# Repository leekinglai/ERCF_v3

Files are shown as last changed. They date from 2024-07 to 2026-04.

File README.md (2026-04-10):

## Carrot Collective Projects

[ERCT / CottonTail Integrated Buffer](https://github.com/Carrot-collective/ERCT)

[Filametrix Toolhead Cutter](https://github.com/Carrot-collective/Filametrix)

[Blobifier Purge System](https://github.com/Carrot-collective/Blobifier)

[Filamentalist Rewinder Buffer](https://github.com/Carrot-collective/Filamentalist)

### Carrot Collective Affiliates

[Jabberwocky Toolhead](https://github.com/kinematicdigit/Jabberwocky)

[Happy Hare Wiki](https://github.com/moggieuk/Happy-Hare/wiki)

<br />

# Enraged Rabbit Community Project

<p align="center">
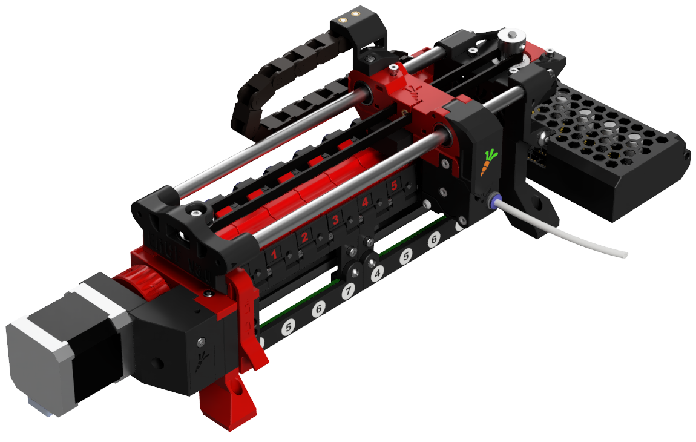
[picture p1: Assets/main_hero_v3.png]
ERCFv3
 
 <h1 align="center">ERCF v3.0</h1>
</p>

<p align="center">
An expandable MMU for Klipper-based 3D-Printers
</p>

<p align="center">
  &nbsp;
  &nbsp;
  &nbsp;
  &nbsp;
  &nbsp;
</p>

<br>

<table>
<tr>
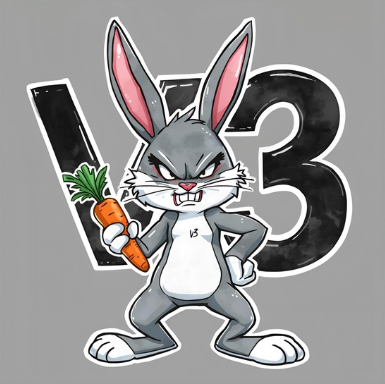
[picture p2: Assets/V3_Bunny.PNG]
Rabbit V3
<td width=30%></td>
<td>
This is a community-born project and a major update to the Voron ERCF MMU that was started a couple of years ago by Ette. It is endorsed by Ette, and the guiding philosophy wasn't to start again with a new MMU design but to refine what has already proven to be a very capable machine and push it to be the best it can be by simplifying problematic construction, improving reliability and aligning as close as possible to v2.0 BOM. The project includes an optional integrated filament buffer system (ERCT), filament cutter option (ERF), a collection of recommended tool head sensor modifications and a bit of Bling! It fully leverages the Happy Hare firmware MMU control software with Klipper Screen extensions.
<p>
 
There is a rapidly growing list of MMUs in the marketplace, from the mass-produced "Fords" who pioneered the market to the "Toyota" that are more recent efficient engineering feat but somehow lacked soul. We consider ERCFv3.0 the "BMW" - a little over-engineered perhaps but distinctively cool, and you feel good driving it. We hope you enjoy it!
</td>
</tr>
</table>

## Table of Content
 
**[ERCF](#enraged-rabbit-carrot-feeder-ercf)**<br>
**[ERCT](#-enraged-rabbit-cotton-tail-erct---filament-buffer)**<br>
**[ERF](#-toolhead-cutter-enraged-rabbit-filametrix-erf)**<br>
**[Toolhead Sensor Modifications](#-toolhead-cutter-enraged-rabbit-filametrix-erf)**<br>
**[Firmware](#firmware)**<br>
**[Documentation](#documentation)**<br>
**[BOM](#bom)**<br>
**[CAD](#cad)**<br>
**[FAQ](#faq)**<br>
**[Acknowledgements](#acknowledgements)**<br>
**[Vendors](#vendors)**<br>
**[Changelog](#changelog)**<br>
**[Build Photos](#build-photos)**<br>
**[Showroom](#user-print-showroom)**<br>
<!--
**[FAQ](Assets/FAQ.md)
-->

<br>

## Enraged Rabbit Carrot Feeder (ERCF)
<table>
<tr>
<td width=45%>An MMU or Multimaterial Unit/Upgrade allows for the automatic change of filaments on your 3D printer. You can use it to create beautiful multi-colored prints or, if you're lazy, simply to avoid loading filament by hand. If you are familiar with ERCF v1.1, this will serve as an overview of updates in v2:</td>
<td>
<ol>
 <li>Sturdy backbone - no more flex</li>
 <li>Reliable (and custom) encoder design</li>
 <li>Sprung servo instead of adjustable top hats</li>
 <li>Innovative Filament trap in blocks instead of magnetic gates</li>
 <li>Formal filament bypass</li>
 <li>Reinforced gearbox assembly</li>
 <li>Beautifully illustrated Manual</li></li>
 <li>High Quality Step-by-step CAD</li>
 <li>Integrated passive buffer system (Cotton Tail)</li>
 <li>Perfect tips with Filametrix Filament cutter</li>
 <li>Functional and aesthetic LED status indication</li>
</ol>
</td>
</tr>
</table>
New features in v3.0 include:
<ol>
 <li>New Direct Drive motor system optimized for torque and ease of use</li>
 <li>Redesigned Gearbox that supports legacy gearing options for upgraders</li>
 <li>Redesigned high-constraint filament blocks with pregate sensors as a default option</li>
 <li>Many Quality of Life additions such as improved Encoder and Selector Cart</li>
 <li>optional microswitch PCBs which allow solderless installation</li>
 <li>optional LED PCBs which allow solderless installation</li>
 <li>Detailed MMB v1.1 and v2.0 wiring diagrams</li>
 <li>Software Setup Documentation for the most popular boards</li>
 <li>Proper GitHub sections for User Mods, Mounting, and PCBs for the community to build upon</li>
 <li>Electronics boxes for the most popular boards: MMBv1 and v2, EasyBRD, ERB*</li>
</ol>

*The ERB is not recommended for use without an additional external 5v power supply.
<br>

## Optional Enraged Rabbit Components

The ERCF ecosystem includes several options to allow you to customize to your specific needs:

#### Filament Buffer/Rewinder Systems
When an MMU changes tool, the unloaded filament needs to be thoughtfully managed so that it doesn't tangle. The ERCF project provides two such systems. The best choice for you will depend on your specific setup:

<br>

###  Enraged Rabbit Cotton Tail (ERCT) - Filament Buffer
<table>
<tr>
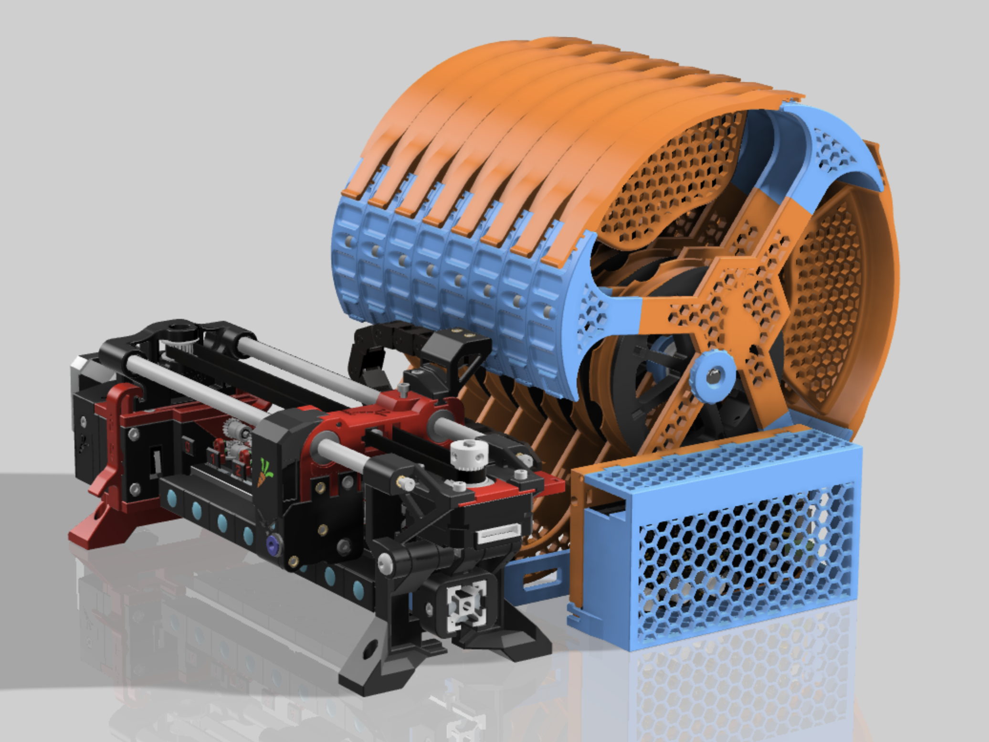
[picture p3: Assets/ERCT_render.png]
ERCT
<td width=30%></td>
<td>
The Enraged Rabbit Cotton Tail (ERCT) buffer system is designed to attach directly to ERCF v3.0. It is a passive system that optimizes space and is also designed to reduce resistance in the filament path, creating a consistent system for calibration.
<p>

ERCT includes a pre-gate filament sensor for automated filament loading and detect runout for endless spool feature. It also incorporates a NEOpixel on each gate that, when driven by the Happy Hare firmware, provides functional feedback and the necessary "bling!"
<p>

ERCT is a very compact and integrated buffer system that is great when your spools are remote from your printer.
<p>

[Read more](https://github.com/Carrot-collective/ERCT) &nbsp;&nbsp; Videos: [Rear Loading](https://youtu.be/9jzB5Un6HKo) [Front Loading](https://youtu.be/GlSXtUkd-b8)
</td>
</tr>
</table>

<br>

###  Enraged Rabbit Filamentalist - Filament Rewinder
<table>
<tr>
<td>
The Enraged Rabbit Filamentalist is an combined solution for buffering AND spool holder and thus provides total space savings. Rather than containing the unwound coils of filament it instead rewinds the filament back onto the spool which means there are never loose filament coils to tangle.
<p>

Filamentalist requires no additional motors because of its innovation of using the gear stepper of the MMU coupled through the filament to power both feeding and rewinding the spool. This can help overcome friction but caution is recommended for really soft TPU.
<p>

Filamentalist can also use the modular pre-gate filament sensor and gate entry LED blocks from ERCT so you don't give up on bling!
<p>

[Read more](https://github.com/Carrot-collective/Filamentalist)
</td>
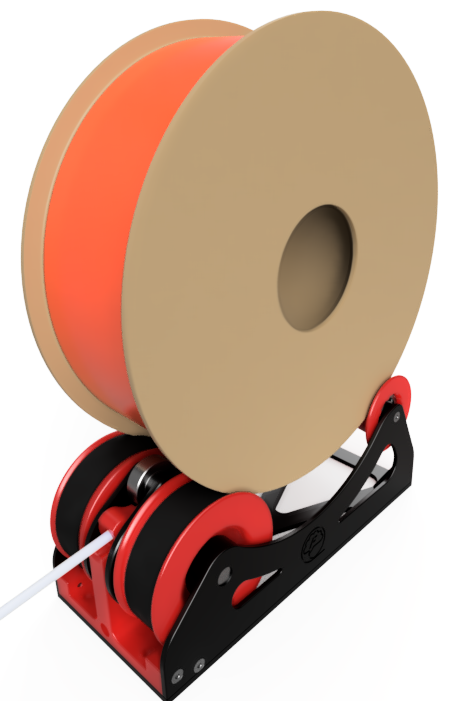
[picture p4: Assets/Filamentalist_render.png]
Filamentalist
<td width=30%></td>
</tr>
</table>

<br>

###  Toolhead Cutter: Enraged Rabbit Filametrix (ERF)
<table>
<tr>
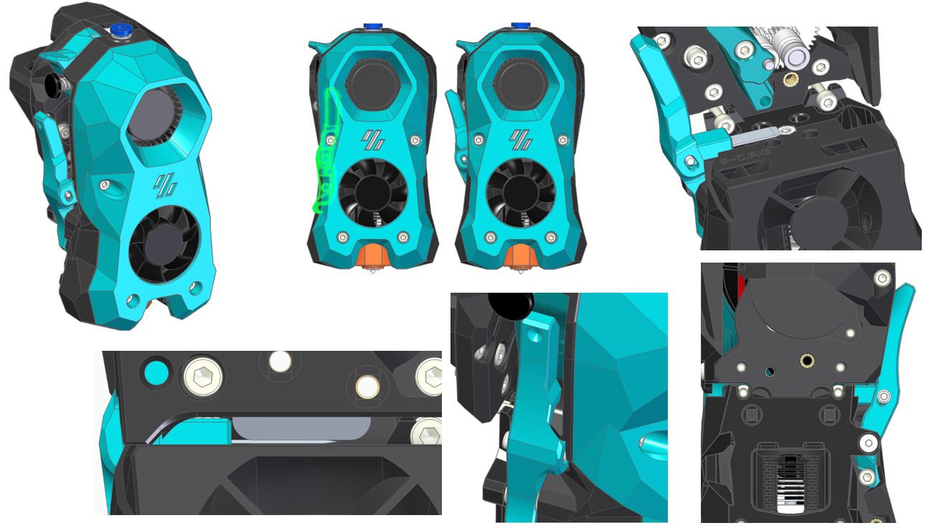
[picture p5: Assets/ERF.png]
ERF
<td width=30%></td>
<td>
Before the MMU can unload a filament, the tip must be prepared so that it can be cleanly loaded next time. This tip-forming process is very difficult to tune and varies based on material type, temperature, hotend type and even weather! Introducing Enraged Rabbit Filametrix (ERF) filament cutting system. This lightweight addition to your Stealthburner toolhead adds a cutting blade. When retracting, the problematic tip of the filament is simply cut off for perfect tips and no jams.
<p>

ERF also supports an optional servo operated ganrtry activation pin so no print area is lost with this addition. ERF designs also include the recommended integrated toolhead sensor
<p>

[Read more](https://github.com/Carrot-collective/Filametrix)
</td>
</tr>
</table>

<br>

###  Toolhead Sensor Modifications
<table>
<tr>
<td>
ERCF can be operated without a toolhead sensor (filament detection) in the toolhead but it is **not recommended**. A toolhead sensor provides an accurate homing point very close to the nozzle but also adds reliability to the tool change process. ERCF includes a set of toolhead sensor modifications for popular extruders. These work reliably through coupling a microswitch to the filament path.
<p>

[Read more](Recommended_Options/README.md)
</td>
</tr>
</table>

<br>

### Purge System (Blobifier)
<table>
<tr>
<td width=30%>Blobifier</td>
<td>

The Blobifier is a small device that eliminates the need for a purgeblock, making filament swaps quicker. It does this by extruding filament onto a tray creating a blob that will get ejected into a purge-bucket.<br />

<h3>Features</h3>

- Turn your filament purge into blobs for less waste and quicker purging.<br />
- Store the blobs in a bucket that can hold 400 blobs!<br />
- Automatically pause the printer once the bucket is full.<br />
- Detect when the bucket is installed or missing.<br />
- Shake the bucket for better dispersion of the blobs in the bucket.<br />
- Clean your nozzle on a brass brush before resuming to print.<br />

[Read More](https://github.com/Carrot-collective/Blobifier)

</td>
</tr>
</table>

<br>

## Firmware
<table>
<tr>
<td width=30%>KlipperScreen</td>
<td>
ERCF is designed to be used with the Happy Hare MMU firmware for Klipper which adds a set of klipper extensions for configuration setup, testing and operation of ERCF. These commands are available through the command line or macros but are perhaps best operated with an interactive UI with the optional KlipperScreen extension.
<p>

Happy Hare provides an easy installation script which has knowledge of recommended settings and will greatly accelerate the setup process.
<p>

[Happy Hare](https://github.com/moggieuk/Happy-Hare/wiki) &nbsp;&nbsp; [KlipperScreen HH Edition](https://github.com/moggieuk/KlipperScreen-Happy-Hare-Edition)
</td>
</tr>
</table>

<br>

## Documentation
<table>
<tr>
<td>
Building something as complex as an MMU is a challenging undertaking, but the ERCFv3.0 project contains an amazingly detailed and illustrated manual with step-by-step instructions. We have tried to make the process similar to fitting together a jigsaw puzzle, albeit with a few optional pieces.
<p>

[Documentation](Documentation)
[Get the latest version of the ERCFv3.0 PDF Manual](Documentation)
</td>
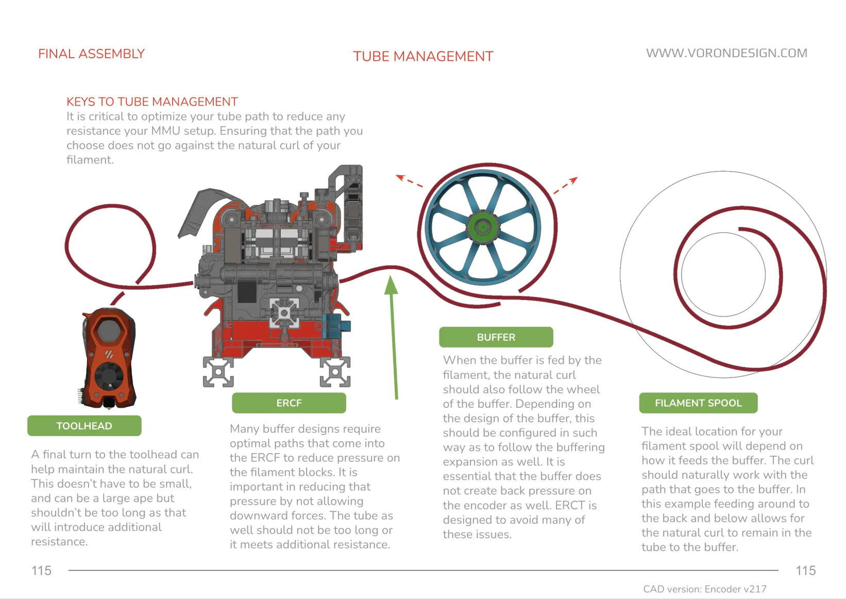
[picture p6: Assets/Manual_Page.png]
ERCF Manual
<td width=30%></td>
</tr>
</table>

<br>

## BOM
<table>
<tr>
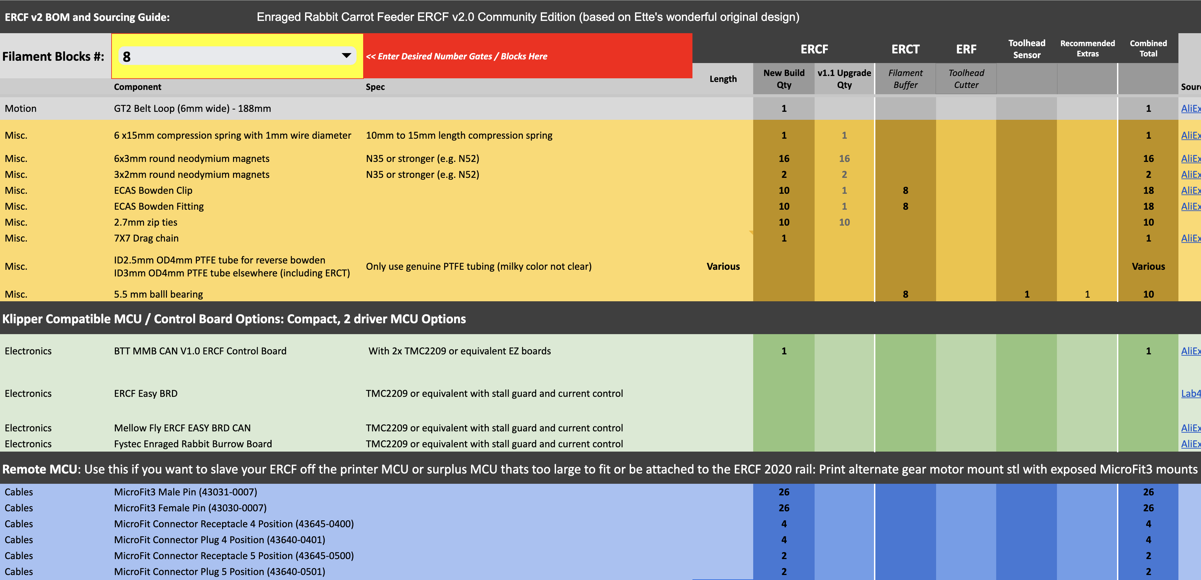
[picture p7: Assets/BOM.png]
ERCF Project BOM
<td width=30%></td>
<td>
You can find a Bill of Materials (BOM) and a convenient printed parts tracker for the project and options here. Note that the BOM also contains an upgrade list for those of you who want to use your existing ERCF v1.1 kits. Please make a copy and edit the "Filament Blocks #" to be the number of gates for your build. This can be any number, but we encourage kit vendors to use 4/8/12 as size variations. Note that there are separate columns for core ERCF, the optional ERCT and ERF options, as well as the suggested "extras"
<p>
Please be aware that the BOM is strictly for reference. The recommended parts can be exchanged for other similar quality parts. Manufacturers who use the BOM as a reference must submit an application for certification before selling them as ERCF v3.0 kits. Please contact us for certification.

[BOM](https://docs.google.com/spreadsheets/d/1UV0rU5Eo4hZX6hcIlSMzn-18oxGSBlLzFjurV6kf8oU/edit?usp=sharing) &nbsp;&nbsp; [Printed Parts Tracker](https://docs.google.com/spreadsheets/d/1MnmpiGlzxnq3sh8Gv73tNb6P1GbJ26OSJ0_e25pumdo/edit?usp=sharing)
</td>
</tr>
</table>

<br>

## CAD
<table>
<tr>
<td>
A lot of work has gone into creating a quality CAD model of the project, carefully organized into folders that match the documentation! It is highly recommended that you open the CAD and hide every folder and then expose them one at a time as you work through the build.
<p>

[Master CAD](CAD)
</td>
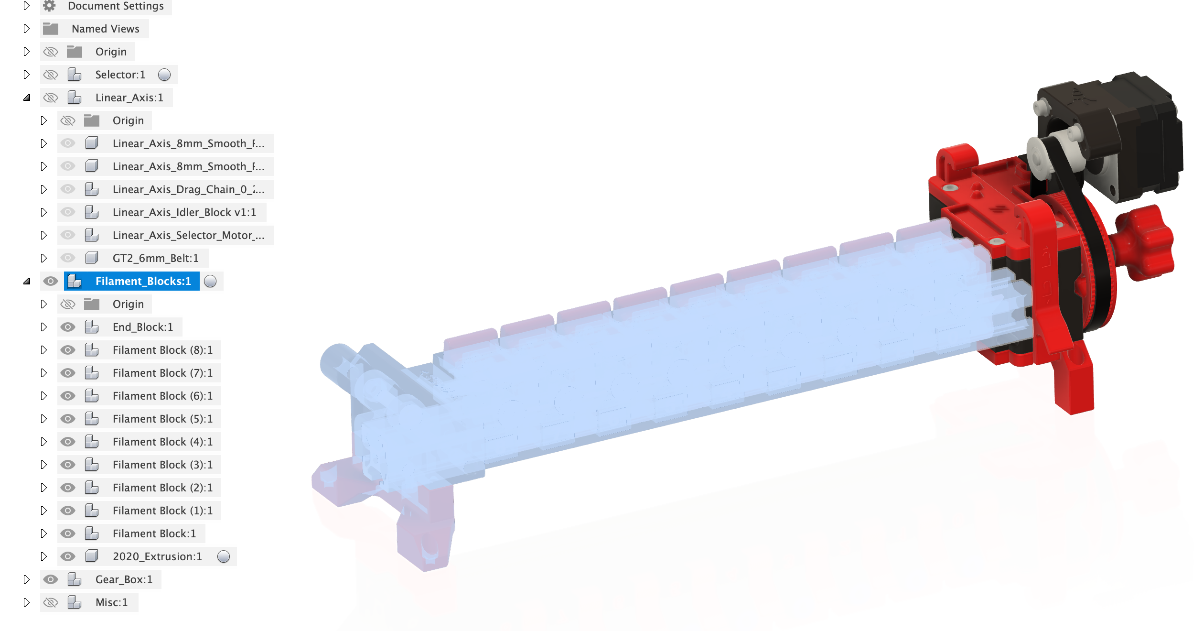
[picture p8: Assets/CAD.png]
ERCF Master CAD
<td width=30%></td>
</tr>
</table>

<br>

## FAQ
ERCF v3 is currently at the fourth iteration or v3.0 phase. Design evolution has required some BOM changes over v2.0. We're sure there will be lots of questions. To avoid repetition on the various support channels, you can find a list of [frequently asked questions](FAQ.md) here. If something isn't answered the best place to go is the primary [ERCF Discord Server](https://discord.gg/t3STJC86HF)

<br>

## Acknowledgements
Most importantly let me introduce the development, test and doc team. A project like this doesn't happen without many hundreds of hours of volunteer effort and all of these folks are truely awesome. Please give some :clap: :clap: :clap:
<ul>
 <li>@Miriax (Designer & Doc Demon)
 <li>@kinematicdigit VS.744 (Designer & Vendor Relations)
 <li>@ningpj (Tester, Breaker & Documenter)
 <li>@SkiBikeMake (Mr Filamentalist)
 <li>@moggieuk V0.1503 | v3.4088 (Mr Happy Hare)
 <li>@gneu v3.0345 (Filament block & bling innovator)
 <li>@sneakytreesnake v3.3804 (The project backbone!)
 <li>@mneuhaus VT.483 (Mr Binky)
 <li>@fizzy (King of CAD)
 <li>@gsx8299 (Test Builder Extraordinaire)
 <li>@sorted (Filametrix "don't get enraged" filament cutting system)
 <li>@kierantheman (Mr ThumperBlocks)
 <li>@Fragmon (Videographer)
 <li>@Silverback v3.1356 (Filametrix tester, builder & engineer)
</ul>

<br>

## Vendors
<table>
<tr>
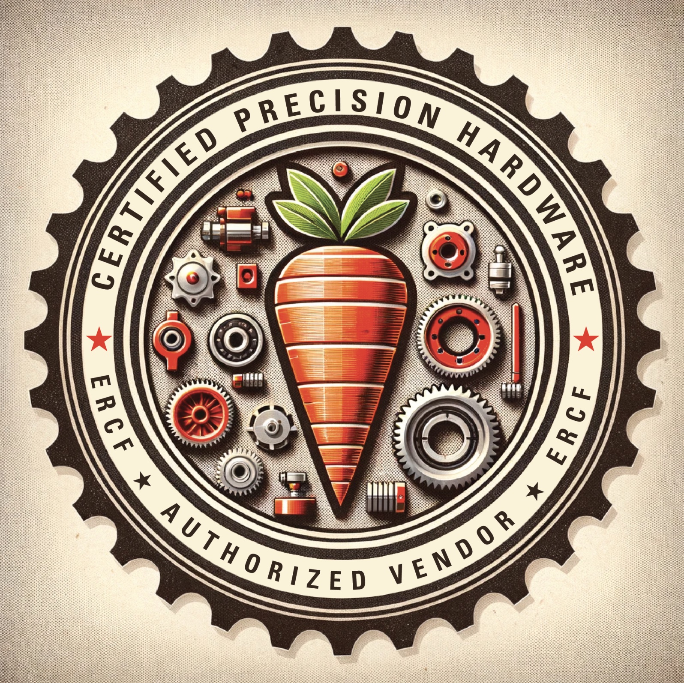
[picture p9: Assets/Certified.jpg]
Vendor Certification
<td width=25%></td>
<td>
These kits and specialty parts will have been checked by us and meet good quality standards. Pending Certification means it has met our first pass inspection and in the process of being verified as a v3 kit. <strong>WE DO NOT RECOMMEND PURCHASING KITS WITHOUT THE CERTIFICATION BY US. PLEASE CHECK BACK HERE FOR THE LIST OF AUTHORIZED VENDORS AND MANUFACTURERS</strong>:<br>
<p>
<ul>
 <li> Approved - Siboor
 </li>
 <li> Pending Submission - Triangle Labs
 </li>
 <li> Approved - <a href="https://www.aliexpress.us/item/3256810002191161.html">Seleadlabs</a>
 </li>
 <li> Pending Submission - Makerpanda
 </li>
 <li> Pending Submission - Fysetc
 </li>
 <li> Approved - <a href="https://www.aliexpress.com/item/1005010543365831.html">Vano3dla 8 channel</a> <a href="https://www.aliexpress.com/item/1005011827763626.html">12 channel</a>
 </li>

 <br>
 <p>
 A list of more official and certified vendors is on the way... stay tuned!
</td>
</tr>
</table>

**Manufacturers:**
_If you want to be included, please contact us. We are happy to validate your kit/parts and then add you to the list._

<br>

## Changelog
<ul>
 <li>v3.0 - Full Release</li>
 <li>v2.0 - Full Release (Happy Easter!)
 <li>v2 RC1 - Initial Release (Happy Christmas!)
</ul>

CAD Design Guidelines used in this project (in case you were interested) can be found: [here](/Assets/Dev_Notes.md).

<hr>

<p align="center"><i>
There once was a printer so keen,<br>
To print in red, yellow, and green.<br>
It whirred and it spun,<br>
Mixing colors for fun,<br>
The most vibrant prints ever seen!
</i></p>

<br>

## Build Photos

Click to enlarge.

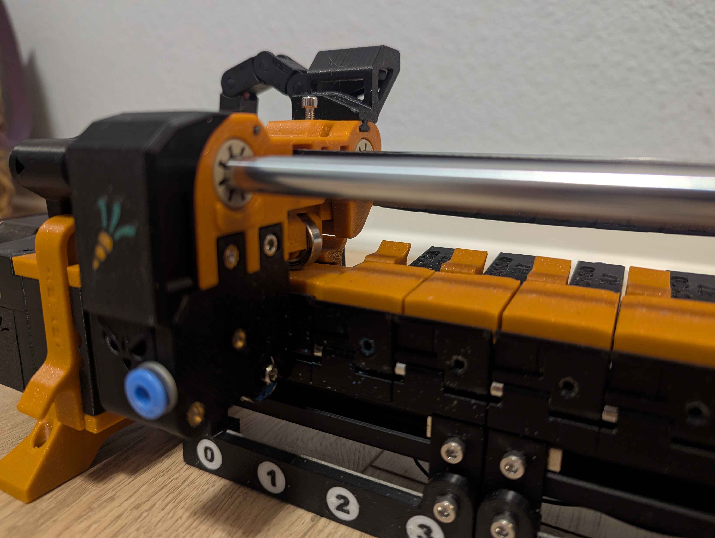
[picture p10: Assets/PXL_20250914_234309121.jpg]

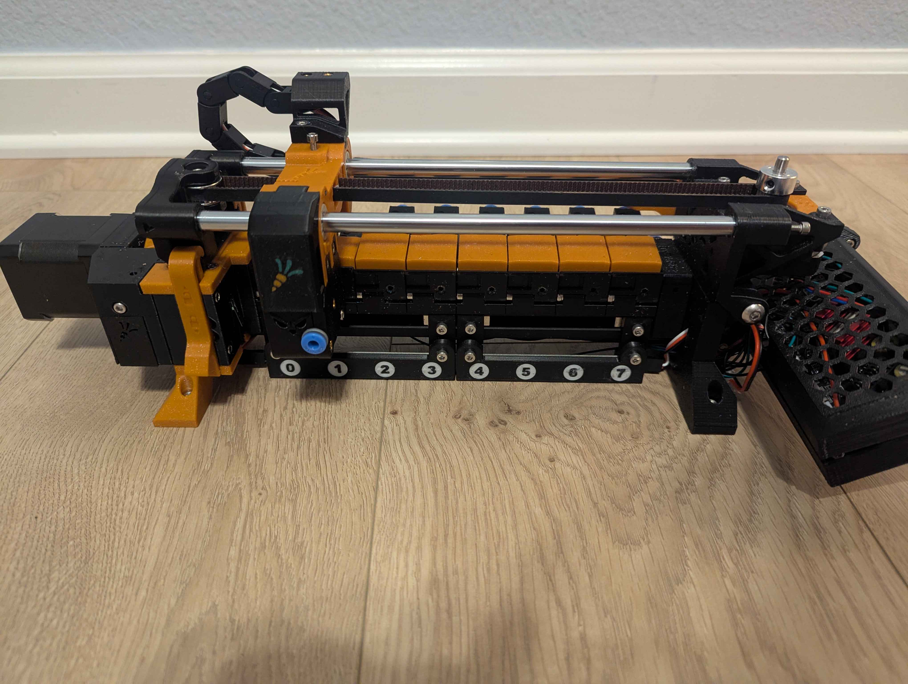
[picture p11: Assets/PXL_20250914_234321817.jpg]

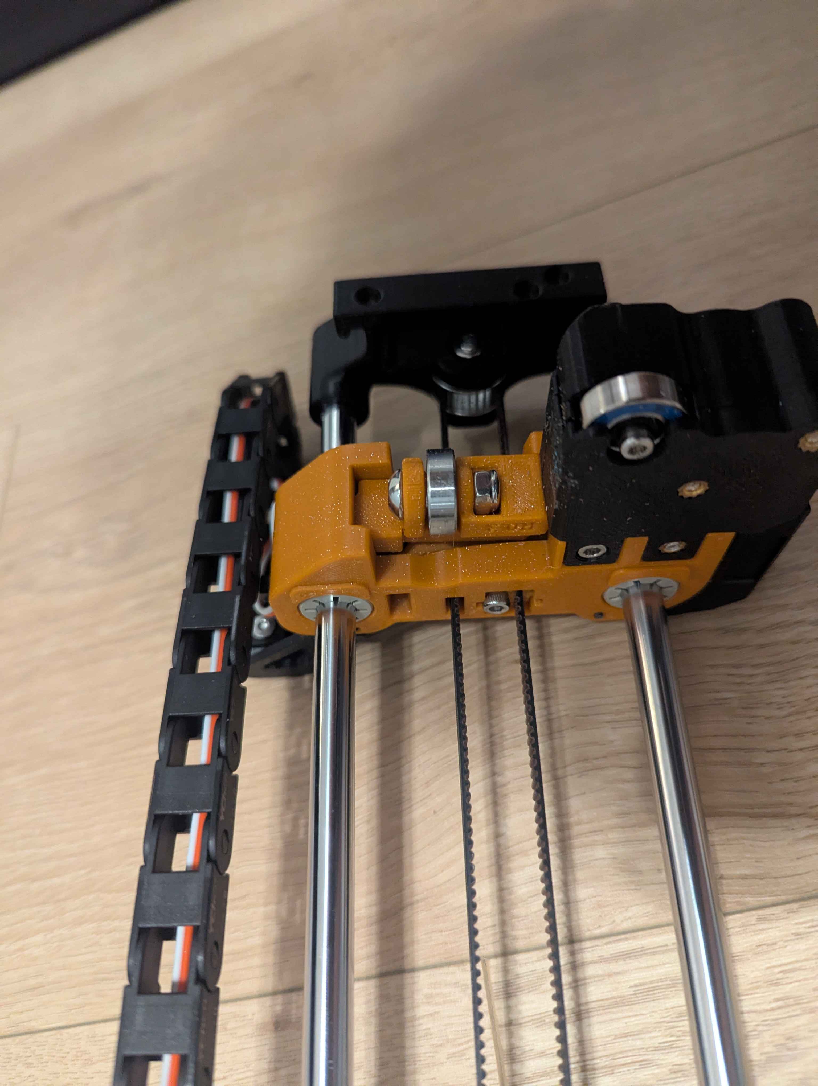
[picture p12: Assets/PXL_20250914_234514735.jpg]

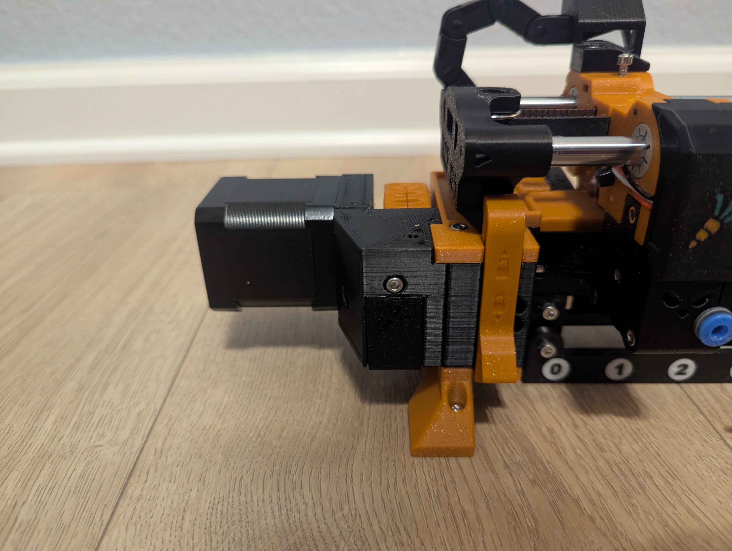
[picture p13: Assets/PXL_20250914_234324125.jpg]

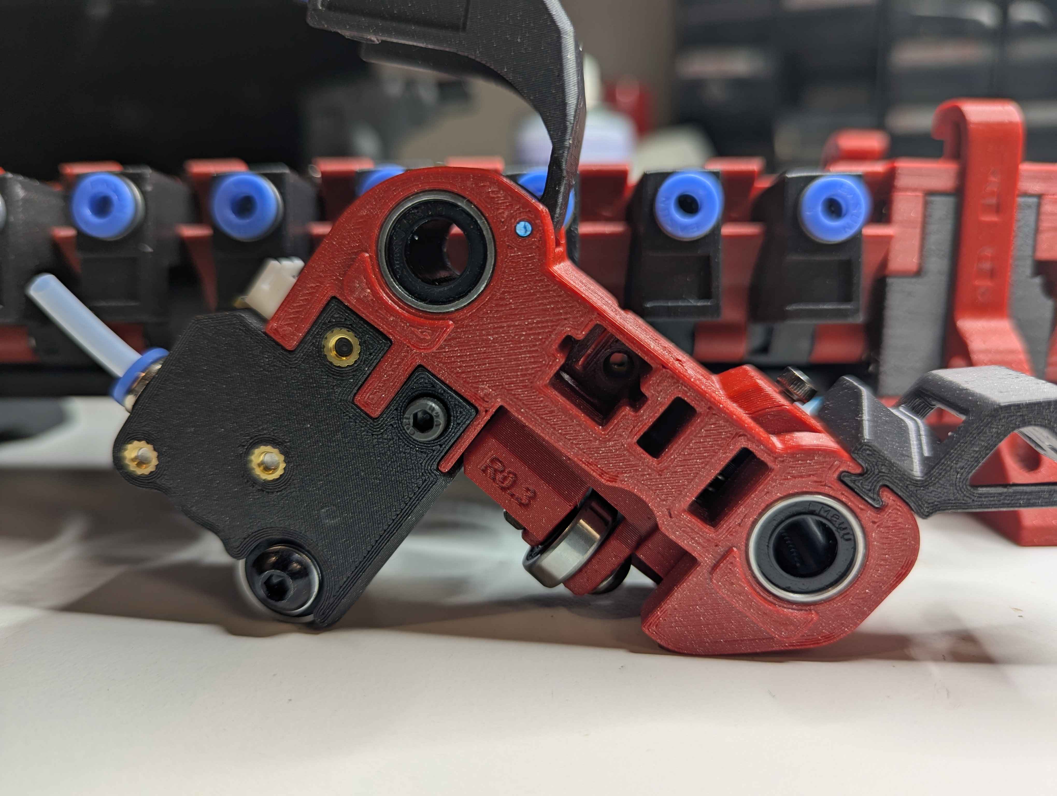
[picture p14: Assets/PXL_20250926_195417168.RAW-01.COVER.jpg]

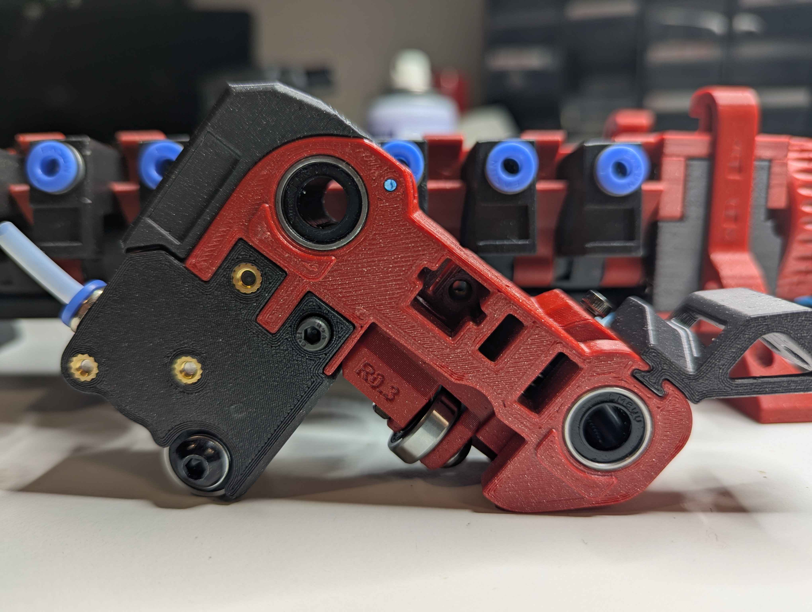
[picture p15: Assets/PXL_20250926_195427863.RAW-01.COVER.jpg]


<br>

## User Print Showroom

Click to enlarge.

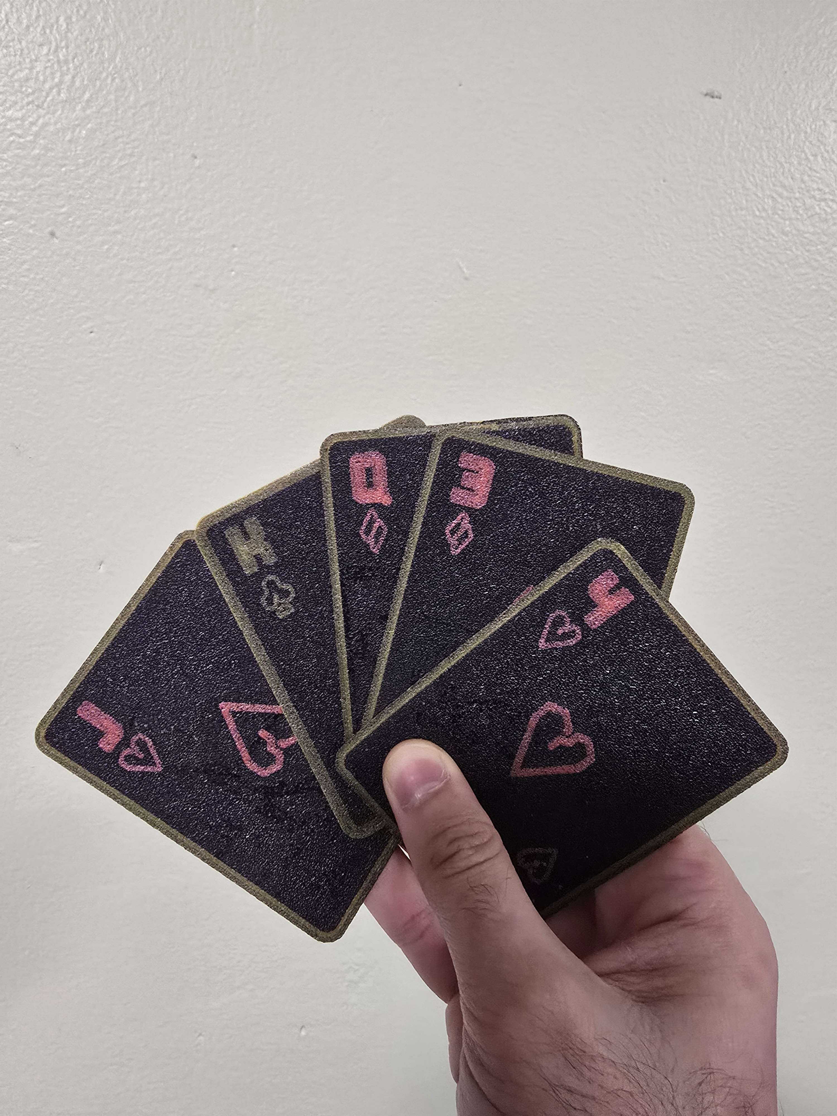
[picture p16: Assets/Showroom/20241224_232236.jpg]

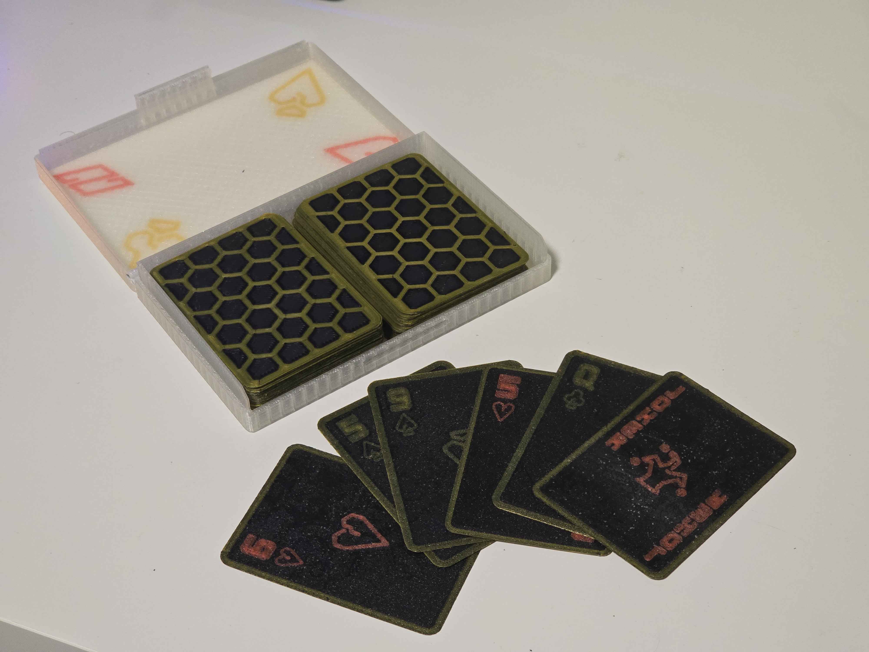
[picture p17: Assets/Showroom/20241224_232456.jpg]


<a href="Assets/Showroom/IMG_4783.png">Gremlin from Mark Norris</a>
<a href="Assets/Showroom/IMG_4783.png">Stormtrooper from Mark Norris</a>

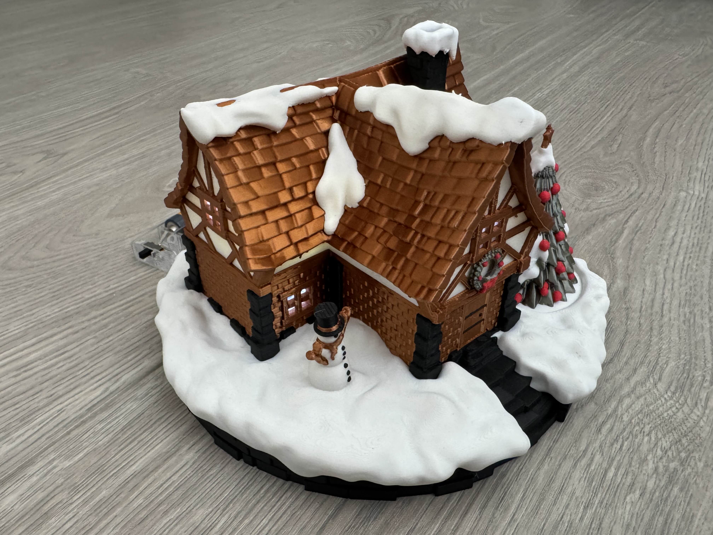
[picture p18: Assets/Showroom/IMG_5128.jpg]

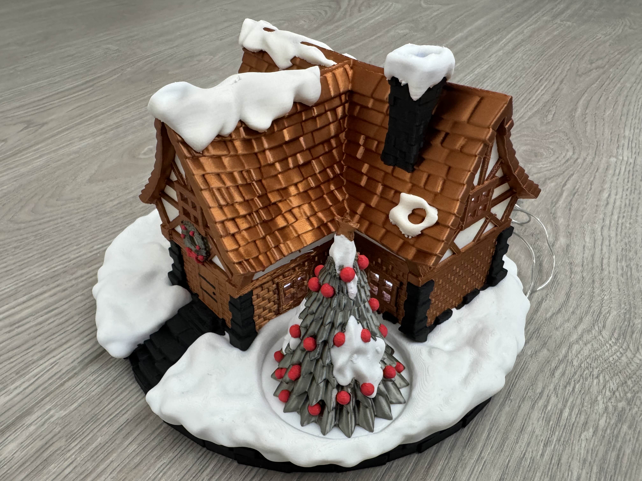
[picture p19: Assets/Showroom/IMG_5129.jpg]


<a href="Assets/Showroom/IMG_5504.jpg">Knit Teddy Bear from Igiannakas</a>
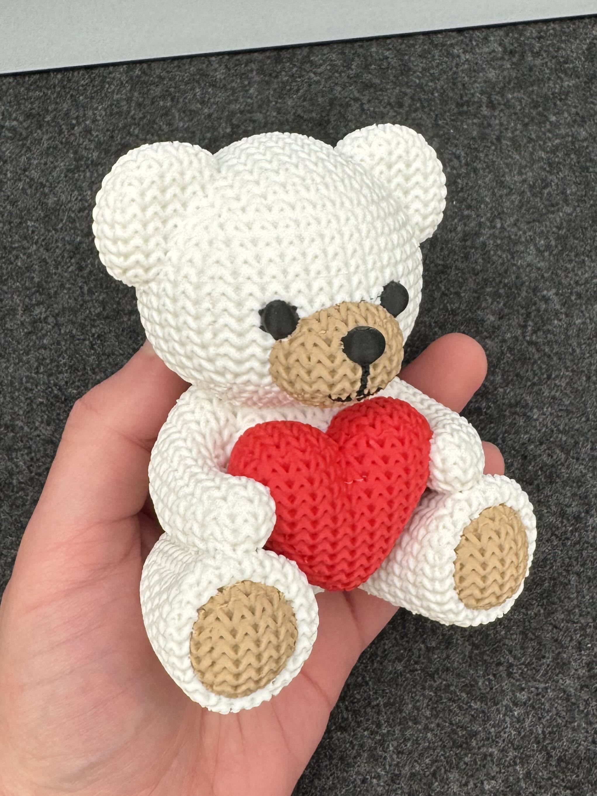
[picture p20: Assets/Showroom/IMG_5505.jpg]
Knit Teddy Bear from Igiannakas


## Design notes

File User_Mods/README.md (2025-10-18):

# ERCF user mod repository

Welcome to ERCF user mod repository. This is a place to share your mods for the ERCF v3 and find useful mods and resources from other ERCF community members.

Mods where the authors have abandoned development can be found in the [`orphaned mods`](./orphaned_mods/) folder. If you want to start maintaining one of them, feel free to reach out via a [GitHub issue](https://github.com/Enraged-Rabbit-Community/ERCF_v3/issues/new/choose).

Looking to submit a mod? Check the [mod submission rules](https://github.com/Enraged-Rabbit-Community/ERCF_v3/blob/main/User_Mods/Mod-Submission-Rules.md) and instructions on [how to submit to ERCF User_Mods](https://github.com/Enraged-Rabbit-Community/ERCF_v3/blob/main/User_Mods/How-to-Submit-to-User-Mods.md)

\[ERCF logo here\]

| Creator | Mod link | Description | Compatibility | Last Changed |
| --- | --- | --- | --- | --- |
| Gneu42 | [Link](Gneu42/Apron_Leds) | Apron LEDs | v2 | Pre-Launch |
| Gneu42 | [Link](Gneu42/Block_End_with_Bushings) | Block End with Bushing | v2 | Pre-Launch |
| Gneu42 | [Link](Gneu42/Drag_Chain_Anchor_With_Microfit3) | Drag Chain Anchor with Microfit3 Connectors | v2, v3 | Pre-launch |
| Gneu42 | [Link](Gneu42/Selector_Drag_chain_Anchor_with_servo_connectors) | Selector Drag Chain Anchor with servo connectors | v2, v3 | Pre-Launch |
| kieraneglin | [Link](https://github.com/Enraged-Rabbit-Community/ERCF_v3/tree/main/User_Mods/kieraneglin/Thumper-Blocks) | Thumper-Blocks | v2 | Pre-Launch
| Miriax | [Link](Miriax/Linear_Axis_Idler_Block_Flipped_Motor) | Flipped Motor Mount for Linear Axis | v2, v3 | Pre-Launch |
| Miriax | [Link](Miriax/Gearbox_for_M6) | Gearbox for M6 Fastener | v3 | Pre-Launch |
| Miriax | [Link](Miriax/Linear_Axis_Idler_Block_for_10mm_Idlers) | Idler Block for 10mm Idlers | v2, v3 | Pre-Launch |
| Miriax | [Link](Miriax/Metal_Coupler_Sleeve) | Metal Coupler Sleeve | v3 | Pre-Launch |
| MNeuhaus | [Link](Mneuhaus/623_Bearing_with_LEDs) | 623 Bearing Encoder with LED | v2 | Pre-Launch |
| MNeuhaus | [Link](Mneuhaus/v623zz_Bearing_with_LEDs) | v623zz Bearing Encoder with LED | v2 | Pre-Launch |
| Batalhoti | [Link](https://github.com/Batalhoti/QuattroSync) | Quattro Sync Tension/Compression Sensor | v2, v3 | 10-18-25 |

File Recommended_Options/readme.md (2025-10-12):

## Recommended Options:

[Filamentalist Rewinder Buffer](https://github.com/Carrot-collective/Filamentalist)

[ERCT / CottonTail Integrated Buffer](https://github.com/Carrot-collective/ERCT)

[Filametrix Toolhead Cutter with Sensors](https://github.com/Carrot-collective/Filametrix)

[Blobifier Purge System](https://github.com/Carrot-collective/Blobifier)

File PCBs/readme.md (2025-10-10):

# PCBs for ERCF

| Creator | PCB link | Description | Compatibility | Last Changed |
| --- | --- | --- | --- | --- |
| Shammy | [Link](Carrot_on_a_Stick) | Carrot on a Stick Apron LEDs | v2, v3 | Pre-Launch |
| Shammy | [Link](Carrot_on_a_Twig) | Carrot on a Twig Apron LEDs | v2, v3 | Pre-Launch |
| TheRogueZeta | [Link](https://github.com/TheRogueZeta/D2F_to_JST_PCB) | D2F to JST PCB | v3 | Pre-Launch |

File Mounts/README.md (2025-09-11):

Mounts for ERCF
---
# ERCF Mounts repository

Welcome to ERCF mounts repository. This is a place to share your mounts for ERCF and find mounts and resources from other ERCF community members.

All mods that apply to older (legacy) ERCF versions can be found in the [`legacy_mounts`](./legacy_mounts) folder.

Looking to submit a mount? Check the [mount submission rules](https://github.com/Enraged-Rabbit-Community/ERCF_v3/blob/main/Mounts/Mount-Submission-Rules.md) and instructions on [how to submit to Mounts](https://github.com/Enraged-Rabbit-Community/ERCF_v3/blob/main/Mounts/How-to-Submit-Mounts.md)

\[ERCF logo here\]

| Creator | Mod link | Description | Compatibility | Last Changed |
| --- | --- | --- | --- | --- |
| Moggieuk | [Link](/Mounts/legacy_mounts/) | Legacy Mounts | v2 | Pre-Launch |

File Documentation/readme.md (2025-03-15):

# ERCF Quickstart

Follow the steps on these pages in order to set up ERCF for the first time!

### ERCF Setup Steps:
- [Flashing Your Local MCU](https://github.com/Enraged-Rabbit-Community/ERCFv2.5/blob/main/Documentation/Flashing-Local-MCU.md)
- [Installing Happy Hare](https://github.com/Enraged-Rabbit-Community/ERCFv2.5/blob/main/Documentation/Installing-Happy-Hare.md)
- [Happy Hare Configuration](https://github.com/Enraged-Rabbit-Community/ERCFv2.5/blob/main/Documentation/Happy-Hare-Configuration.md)
- [Hardware Configuration Checks](https://github.com/Enraged-Rabbit-Community/ERCFv2.5/blob/main/Documentation/Hardware-configuration-checks.md)
- [Hardware Calibration](https://github.com/Enraged-Rabbit-Community/ERCFv2.5/blob/main/Documentation/Hardware-Calibration.md)
- [Toolhead Distances](https://github.com/Enraged-Rabbit-Community/ERCFv2.5/blob/main/Documentation/Toolhead-Distances.md)
- [Installing KlipperScreen Happy Hare](https://github.com/Enraged-Rabbit-Community/ERCFv2.5/blob/main/Documentation/Installing-KlipperScreen.md)
- [Slicer Setup](https://github.com/Enraged-Rabbit-Community/ERCFv2.5/blob/main/Documentation/Slicer-Setup.md)
- [Further Mods to Consider](https://github.com/Enraged-Rabbit-Community/ERCFv2.5/blob/main/Documentation/Further-Mods.md)

#### Even more Happy Hare info can be found at:
- [Happy Hare Wiki](https://github.com/moggieuk/Happy-Hare/wiki)

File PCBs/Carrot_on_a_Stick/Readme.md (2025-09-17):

## Carrot on a Stick LED Board

This board was based on the Disco on a Stick board. The LEDs are spaced 23.05mm, exactly the same as the Filament Blocks, allowing these to be daisy-chained together to make any even number of channels possible with no soldering required!

Thanks to [Blamm!](https://github.com/bartlammers) for allowing us to use his [Disco on a Stick](https://github.com/VoronDesign/Voron-Hardware/tree/master/Daylight/Disco_on_a_stick) design.

Thanks to Shammy and [XR Bunker](https://xrbunker.works/products/carrot-on-a-stick) for modifying the Disco on a Stick design.

Thanks to [Fabreeko](https://www.fabreeko.com/products/carrot-on-a-stick-carrot-on-a-twig-led-boards-for-ercf-v2-0) for being our initial supplier of boards.

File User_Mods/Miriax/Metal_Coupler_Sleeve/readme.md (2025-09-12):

# Metal Coupler Sleeve

Uses 5mm ID "rigid shaft coupling," 20mm long, 12mm diameter, threaded for M4. If you can find one threaded for M3, let me know!

[Amazon.co.jp Link](https://www.amazon.co.jp/dp/B0BZS6CTPC)

[AliExpress Link](https://www.aliexpress.us/item/3256804476993285.html)

[Amazon US Link](https://www.amazon.com/dp/B08V8H721N)

# Print Settings

As normal. Supports are left to the user and not built-in as normal.

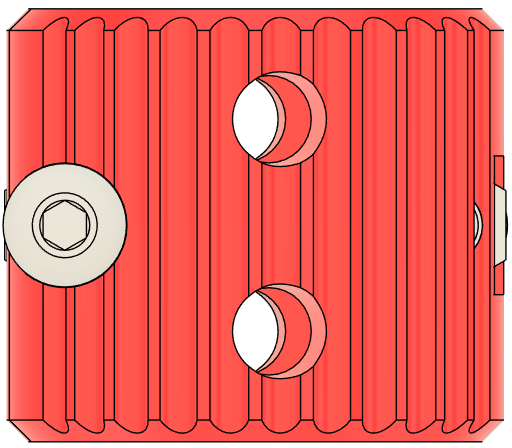
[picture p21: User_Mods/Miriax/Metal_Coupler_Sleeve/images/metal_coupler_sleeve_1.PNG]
coupler angle 1


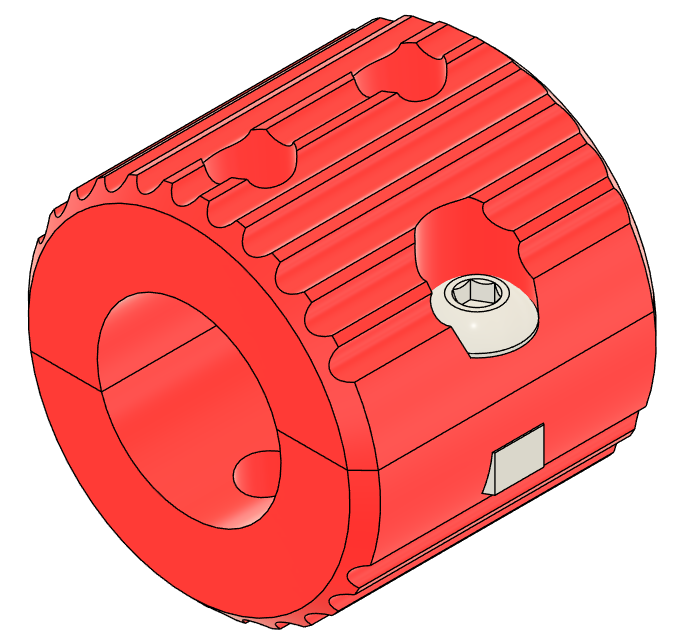
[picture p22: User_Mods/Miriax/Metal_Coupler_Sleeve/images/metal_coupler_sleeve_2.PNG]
coupler angle 2


# Instructions

Insert M3 nut into coupler halves

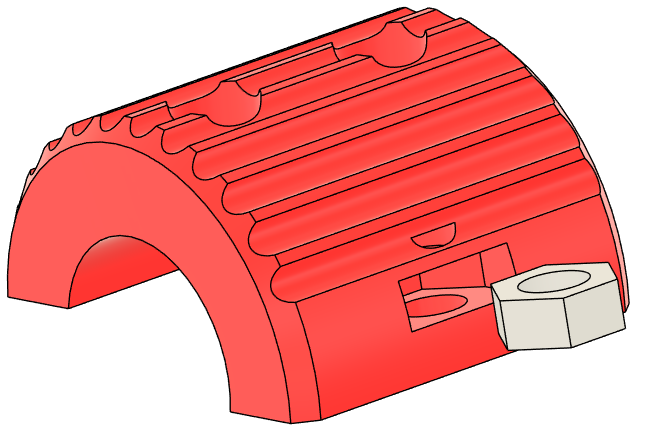
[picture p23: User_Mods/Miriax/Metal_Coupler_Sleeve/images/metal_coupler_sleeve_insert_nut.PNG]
Insert nut into coupler halves


Insert M3x8mm BHCS and snug

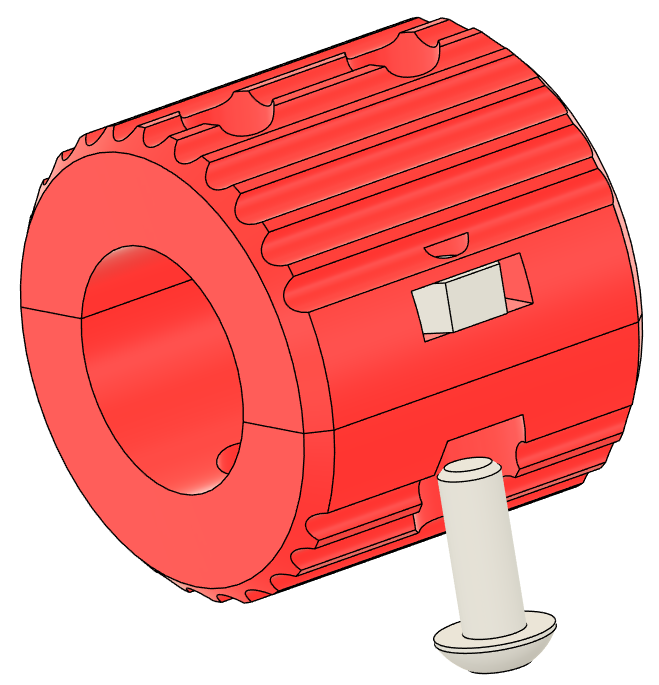
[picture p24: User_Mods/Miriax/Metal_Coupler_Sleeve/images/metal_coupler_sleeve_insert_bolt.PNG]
insert M3x8 bolt and snug


Insert metal coupler. Align the grubscrew holes with the holes in the sleeve. Tighten the bolts, alternating until snug. This only needs to be snug enough to grip the metal coupler.

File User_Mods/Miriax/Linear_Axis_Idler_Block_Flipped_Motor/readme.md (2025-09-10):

This is a Selector Motor mount for Selector motors larger than 20mm. I flipped the motor upside down. It uses all the same hardware. The only difference is that the motor is now 3.8mm closer to the Selector, so you will need to trim ~7.6mm from your belt.

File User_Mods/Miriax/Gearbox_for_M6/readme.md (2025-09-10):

These are Gearboxes for M6 fasteners. One version is for BHCS M6 fasteners (preferred) and the other is for SHCS M6 fasteners.

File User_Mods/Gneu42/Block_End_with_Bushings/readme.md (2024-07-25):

<h1 align="center"><ins>Reinforced Block End </ins></h1>

<H2 align="center">Filament block end with brass bushing and 5mm shaft.</H1>

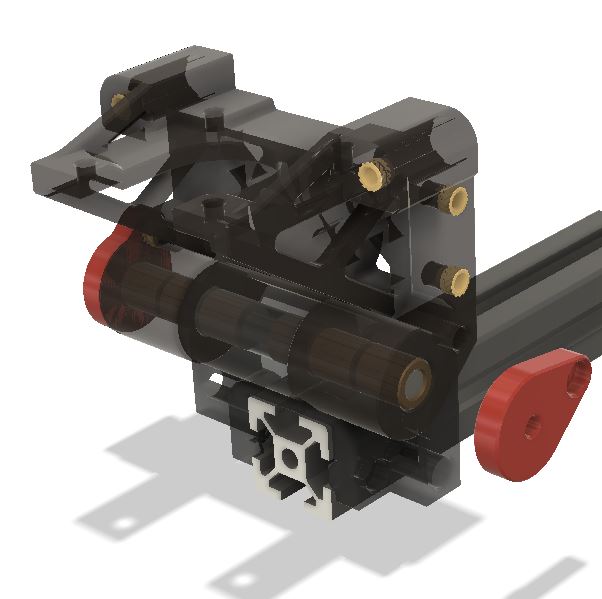
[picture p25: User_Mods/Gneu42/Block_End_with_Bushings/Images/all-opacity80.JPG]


This will give a strong and rigid connection between the top and bottom block end.
It will be very easy to separate the linear axis form the bottom part.
    Just open the exit side Axles stop and push the 5mm shaft with a 2.5mm allen key, and then remove the shaft.

**It will become more useful with the "coming soon" microfit 3 connectors mod that will allow to disconnect the linear axis assembly from the main ERCF.** 

## Bom
In addition to the normal bom for those parts, you will need :
* 2 M3 inserts
* 2 M3x8 SHCS 
* 6 Brass bushings 5x9x10
* 1 Shaft 5mm in diameter, 68mm long.  

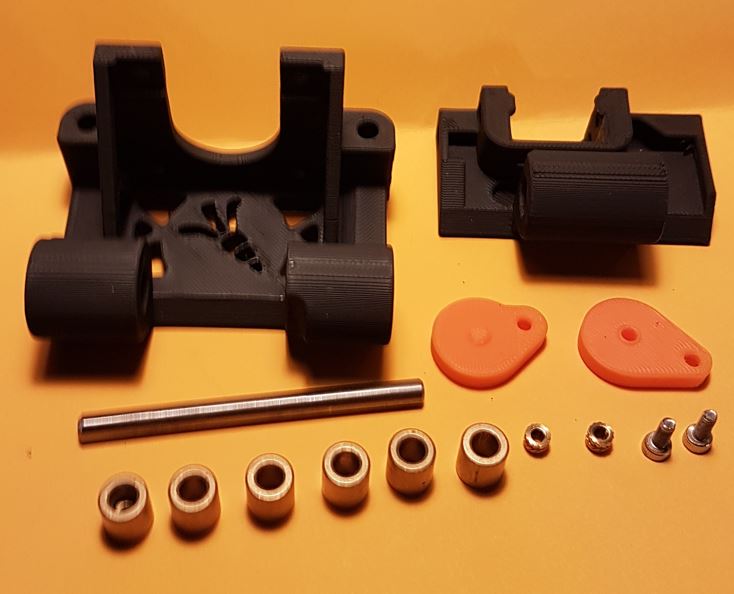
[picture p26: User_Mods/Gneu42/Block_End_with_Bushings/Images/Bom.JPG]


The bushings can be found on Aliexpress : https://fr.aliexpress.com/item/1005004074472637.html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

## Cut view

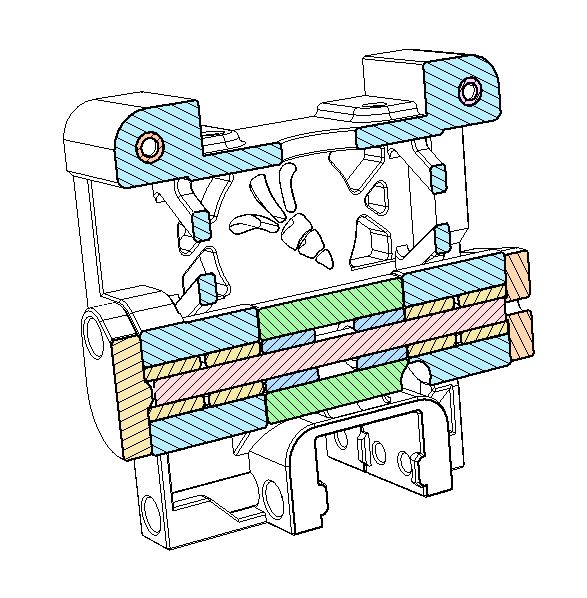
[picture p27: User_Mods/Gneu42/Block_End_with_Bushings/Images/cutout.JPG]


## Images

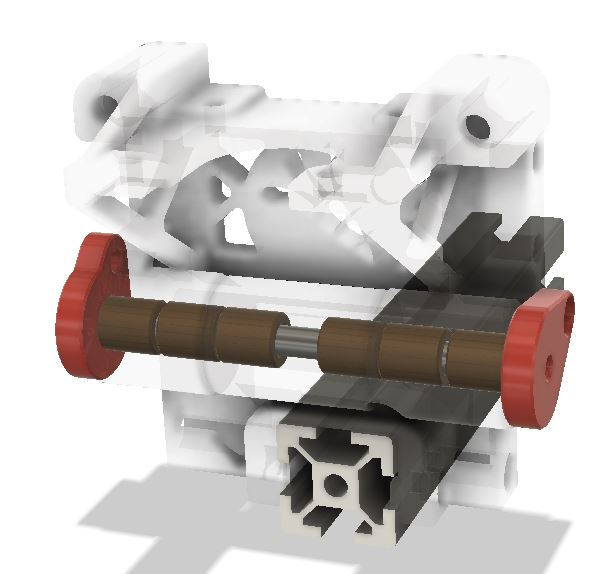
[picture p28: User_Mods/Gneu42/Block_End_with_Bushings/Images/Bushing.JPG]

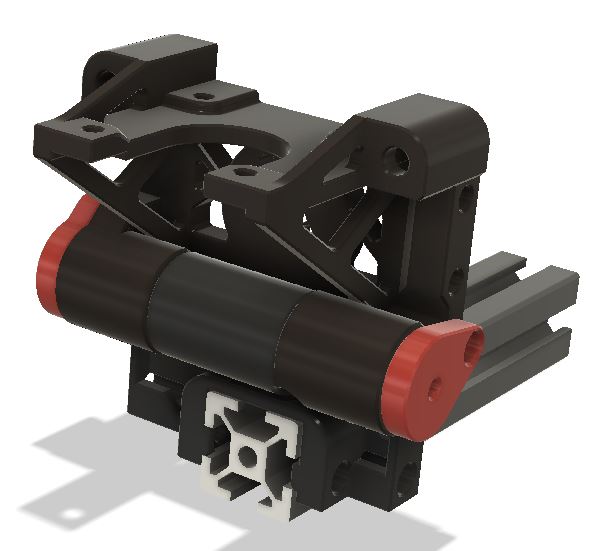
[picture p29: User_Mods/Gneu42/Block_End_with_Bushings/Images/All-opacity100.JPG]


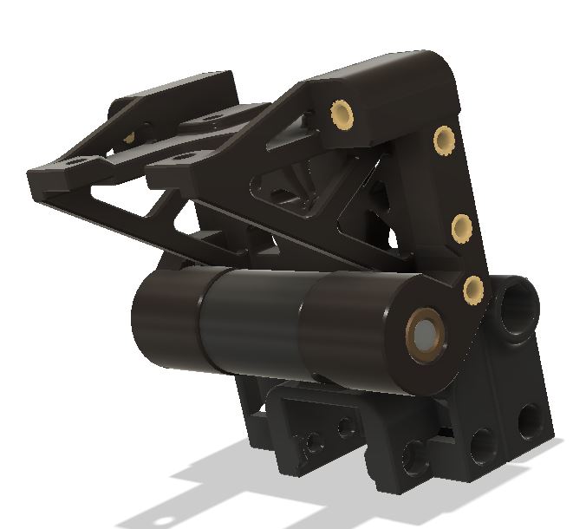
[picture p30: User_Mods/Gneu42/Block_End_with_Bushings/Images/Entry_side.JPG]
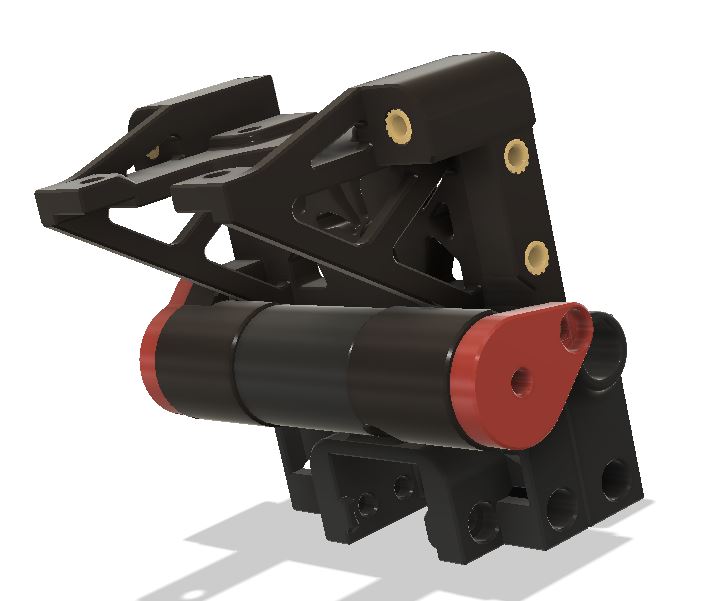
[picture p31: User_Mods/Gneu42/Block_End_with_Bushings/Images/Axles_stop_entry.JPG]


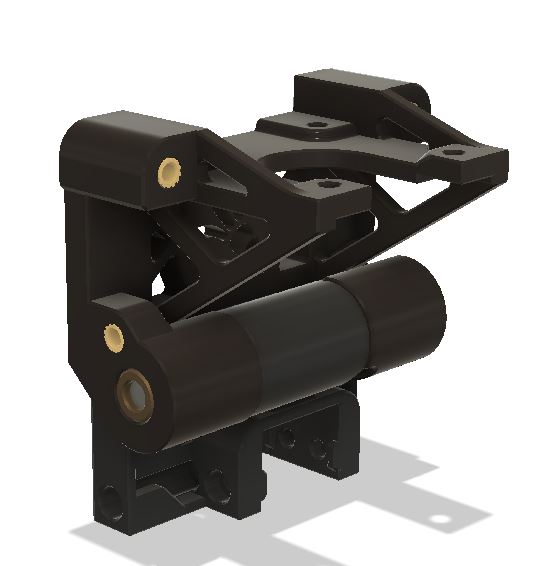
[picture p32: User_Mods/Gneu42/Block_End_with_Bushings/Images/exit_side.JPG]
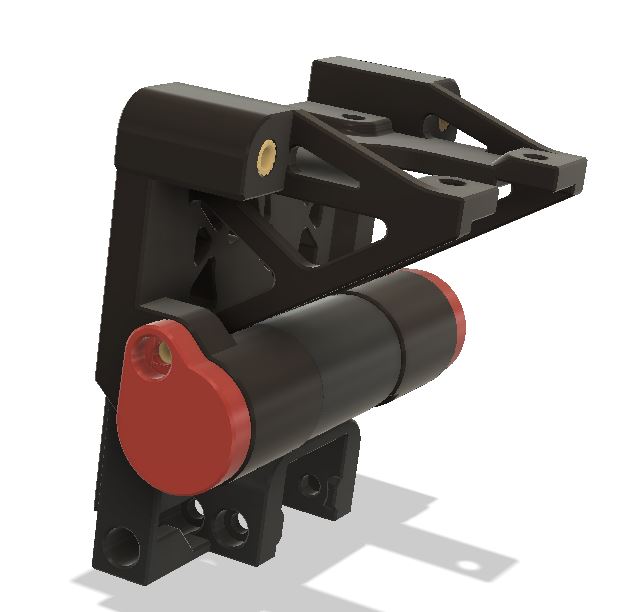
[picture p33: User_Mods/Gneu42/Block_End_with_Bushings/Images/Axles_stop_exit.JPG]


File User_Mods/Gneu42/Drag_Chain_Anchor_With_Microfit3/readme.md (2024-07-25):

<h1 align="center"><ins>Darg chain anchor with Microfit 3 connectors </ins></h1>

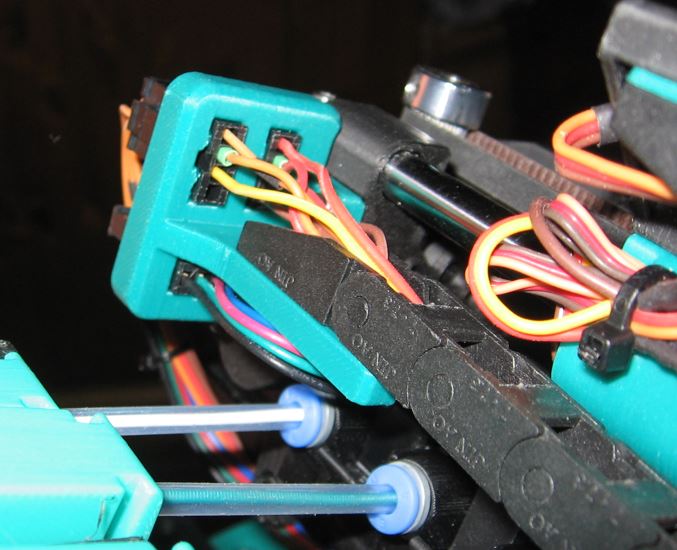
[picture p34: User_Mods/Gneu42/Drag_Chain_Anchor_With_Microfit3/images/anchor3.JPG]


This will allow to very easily remove the top part of the ERCF V2 for maintenance purpose.
It is designed to go with the Block End with bushing mods on this repo.

## Bom
In addition to the normal bom for those parts, you will need :
* 2 M3 inserts
* 2 M3x8 SHCS 
* 3 Microfit 3, 4 pins connector male
* 3 Microfit 3, 4 pins connector female  

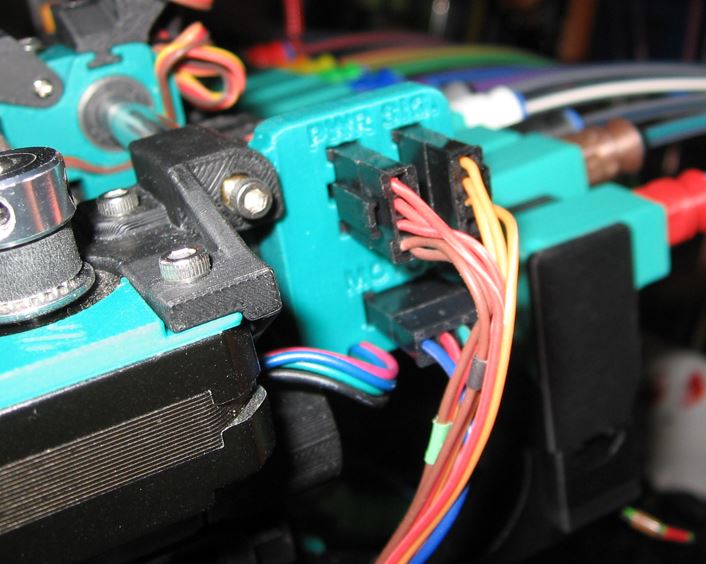
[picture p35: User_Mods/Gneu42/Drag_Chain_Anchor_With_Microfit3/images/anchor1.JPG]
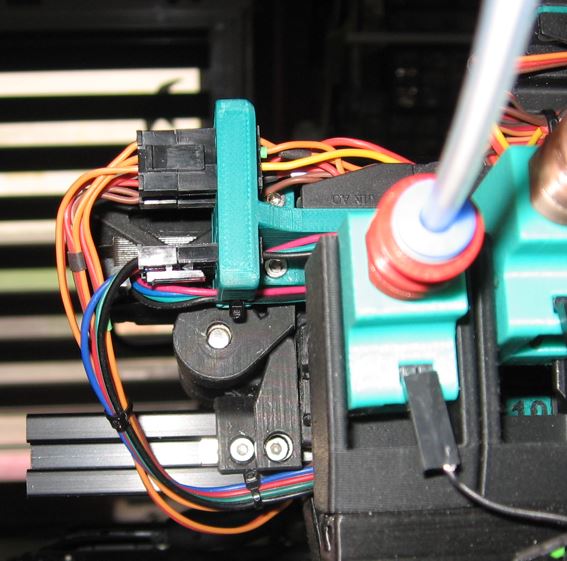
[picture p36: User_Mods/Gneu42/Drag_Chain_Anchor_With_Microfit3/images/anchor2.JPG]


* The connector marked "MOTOR" is used for the motor connection
* The connector marked "PWR" is used for power supply of the Binky encoder, the servo, and the status LED.
* The connector marked "Sig." is used for the signals of the Binky encoder, the servo signal, the status data signal of the status LED, and a spare pin available for what ever you need more. 

**Here is an example of the Microfit3 pinout :**

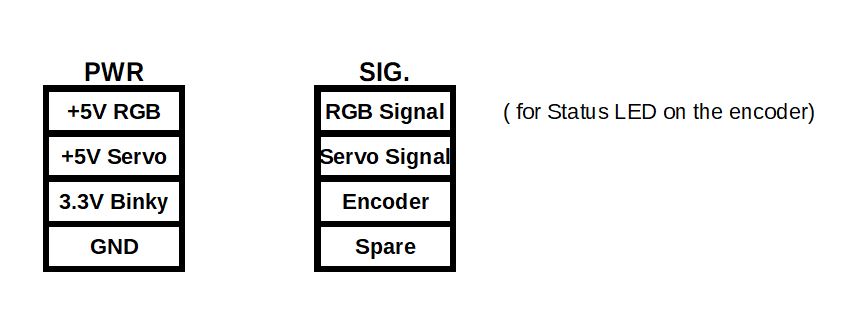
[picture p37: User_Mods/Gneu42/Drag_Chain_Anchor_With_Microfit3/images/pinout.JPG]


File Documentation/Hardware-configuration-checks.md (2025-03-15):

#### Page Sections:
  - [Checks You Should Have Done Already](#checks-you-should-have-done-already)
  - [Step 1. Check Endstop & Optional Sensors](#step-1-check-endstop--optional-sensors)
  - [Step 2. Check motor movement and direction](#step-2-check-motor-movement-and-direction)
  - [Step 3. Check the Encoder](#step-3-check-the-encoder)
  - [Step 4. Check other sensors (if fitted)](#step-4-check-other-sensors-if-fitted)
  - [Step 5. Check Servo](#step-5-check-servo)

*\[This guide was adapted from the [Happy Hare Wiki](https://github.com/moggieuk/Happy-Hare/wiki) for ERCF v2.5. Thanks Moggie!\]*

## Checks You Should Have Done Already

All of these checks and adjustments were covered in the Build Manual, and should have been done while building your ERCF.

-Filament path / BMG Gear alignment (Manual page 71)

-(if using a Geared setup) Adjustment of GT2 pulley and belt tension (Covered in the Geared Drive sub-Manual)

-Encoder path adjustment (page 114)

-Setting GT2 pulley and belt tension (page 127)

-Setting 8mm rod depth (page 136)

**If you haven't done these steps, go review the manual!**

<br>

Now that you've completed the [Happy Hare Configuration](https://github.com/Enraged-Rabbit-Community/ERCFv2.5/blob/main/Documentation/Happy-Hare-Configuration.md), you should be greeted by a large warning on your console:

```yml
Prerequsite calibration steps are not complete:
Use MMU_CALIBRATE_SELECTOR to calibrate selector for gates: 0,1,2,3,4,5,6,7
Use MMU_CALIBRATE_GEAR (with gate 0 selected) to calibrate gear rotation_distance on gate: 0
Use MMU_CALIBRATE_ENCODER (with gate 0 selected)
Use MMU_CALIBRATE_GEAR (with gate selected) or MMU_CALIBRATE_GATES GATE=xx to calibrate gear rotation_distance on gates: 1,2,3,4,5,6,7
Use MMU_CALIBRATE_BOWDEN
```

That is normal, do not worry. Before we tackle that, we need to make sure all of the hardware is configured correctly!

## Step 1. Check Endstop & Optional Sensors

Verify that the Selector endstop, and any installed extruder or toolhead sensors are working. The recommended procedure is:

`MMU_MOTORS_OFF`

Now remove filament from ERCF and extruder, and move the Selector to the center of travel.

`QUERY_ENDSTOPS`

(Or use the visual query in Mainsail or Fluuid). Validate that you can see:

```yml
mmu_sel_home:open
extruder:open
toolhead:open
[...]
```

> [!NOTE]
> You will only see the sensors you have installed. You will additionally see any endstops or sensors installed on your printer.

Then manually press and hold the selector microswitch and rerun `QUERY_ENDSTOPS`.

Validate that you can see `mmu_sel_home:TRIGGERED` in the list.

If you have an extruder sensor installed, feed filament into the extruder past the switch and rerun `QUERY_ENDSTOPS`.

Validate that you can see `extruder:TRIGGERED` in the list.

If you have a toolhead sensor installed, feed filament into the toolhead past the switch and rerun `QUERY_ENDSTOPS`.

Validate that you can see `toolhead:TRIGGERED` in the list.

If any of these don't change state, then the pin assigned to the endstop is incorrect. If the state is inverted (i.e. enstop transitions to `open` when pressed) then add/remove the `!` on the respective endstop pin in `mmu_hardware.cfg`. 

Other endstops like "touch" operation and pregate sensors are advanced and are not cover by this inital setup.

## Step 2. Check motor movement and direction

Once pins are correct it is important to verify direction.  It is not possible for the installer to ensure this because it depends on the actual stepper wiring.  The recommended procedure is:

Run the command `MMU_MOTORS_OFF` Now move the Selector to the center of travel. 

Next, run the command `MMU_HOME` and verify that the Selector moves towards the endstop / home position

If the Selector doesn't move it is likley that the pin configuration for `step_pin` and/or `enable_pin` are incorrect. Open up `mmu_hardware.cfg`, and find the section `[stepper_mmu_selector]`.

Verify the pin names and prefix the pin with `!` to invert the signal. E.g.

```yml
enable_pin: !mmu:MMU_SEL_ENABLE
 (or)
enable_pin: mmu:MMU_SEL_ENABLE
```

If the selector moves the wrong way the `dir_pin` is inverted. Either add or remove the `!` prefix:

```yml
dir_pin: !mmu:MMU_SEL_DIR
 (or)
dir_pin: mmu:MMU_SEL_DIR
```

Now repeat the exercise with the gear stepper:

```yml
MMU_MOTORS_OFF
  (remove any filament from your MMU)
MMU_TEST_MOVE MOVE=100 SPEED=50
  (verify that the gear stepper would push filament towards the extruder / pull filament from the spool)
MMU_TEST_MOVE MOVE=-100 SPEED=50
  (verify that the gear stepper is pulling filament away from the extruder / pushing filament back to the spool)
```

If the gear stepper doesn't move or moves the wrong way open up `mmu_hardware.cfg`, find the section `[stepper_mmu_gear]`:<br>
If gear doesn't move it is likley that the pin configuration for `step_pin` and/or `enable_pin` are incorrect. Verify the pin names and prefix the pin with `!` to invert the signal. E.g.

```yml
enable_pin: !mmu:MMU_GEAR_ENABLE
 (or)
enable_pin: mmu:MMU_GEAR_ENABLE
```

If the gear moves the wrong way the `dir_pin` is inverted. Either add or remove the `!` prefix:

```yml
dir_pin: !mmu:MMU_GEAR_DIR
  # or
dir_pin: mmu:MMU_GEAR_DIR
```

## Step 3. Check the Encoder

We need to check that the Encoder is wired correctly. Run the command `MMU_ENCODER` and note the position displayed.

```yml
MMU_ENCODER
Encoder position: 23.4
```

Insert some filament (from either side) and pull backwards and forwards.  You should see the red LED flashing behind the enraged rabbit's eyes. Rerun `MMU_ENCODER` and validate the position displayed has increased (note that the encoder is not direction aware, so it will always increase in reading).

If the encoder postion does not change, validate the `encoder_pin` is correct. It shouldn't matter if it has a `!` (inverted) or not, but it might require a `^` (pull up resister) to function.

```yml
[mmu_encoder mmu_encoder]
encoder_pin: ^mmu:MMU_ENCODER	
```

## Step 4. Check other sensors (if fitted)

Other sensors are generally filament sensors and act on a switch. The easiest way to check these is to run something similar to the following for each sensor/switch.

```yml
QUERY_FILAMENT_SENSOR SENSOR=mmu_gate_sensor
Filament Sensor mmu_gate_sensor: filament not detected
```

Activate the sensor with a piece of filament and run again:

```yml
QUERY_FILAMENT_SENSOR SENSOR=mmu_gate_sensor
Filament Sensor mmu_gate_sensor: filament detected
```

Note that endstops / filament sensors that are wired normally open (NO) frequently require `^` (pull up resister) to correctly function.

## Step 5. Check Servo

> [!IMPORTANT] 
> The Servo Arm should *not* be installed yet for this test!

Ok, last sanity check. Check that the servo you have fitted is operational. Run this simple commmand. The servo should wiggle somewhere short of the configured 'up' and 'down' positions. Don't worry yet about calibration. That comes next.

```yml
MMU_TEST_BUZZ_MOTOR MOTOR=servo
```

You can also try:
```yml
MMU_SERVO POS=down
MMU_SERVO POS=up
```

All we are checking is that the servo is wired and operational.

> [!NOTE] 
> It is normal for the Gear motor to move back and forth slightly during a `MMU_SERVO POS=down` command. This is to ensure that the BMG gears mesh properly.

### ERCF Setup Steps:
- [Flashing Your Local MCU](https://github.com/Enraged-Rabbit-Community/ERCFv2.5/blob/main/Documentation/Flashing-Local-MCU.md)
- [Installing Happy Hare](https://github.com/Enraged-Rabbit-Community/ERCFv2.5/blob/main/Documentation/Installing-Happy-Hare.md)
- [Happy Hare Configuration](https://github.com/Enraged-Rabbit-Community/ERCFv2.5/blob/main/Documentation/Happy-Hare-Configuration.md)
- Hardware Configuration Checks
- [Hardware Calibration](https://github.com/Enraged-Rabbit-Community/ERCFv2.5/blob/main/Documentation/Hardware-Calibration.md)
- [Toolhead Distances](https://github.com/Enraged-Rabbit-Community/ERCFv2.5/blob/main/Documentation/Toolhead-Distances.md)
- [Installing KlipperScreen Happy Hare](https://github.com/Enraged-Rabbit-Community/ERCFv2.5/blob/main/Documentation/Installing-KlipperScreen.md)
- [Slicer Setup](https://github.com/Enraged-Rabbit-Community/ERCFv2.5/blob/main/Documentation/Slicer-Setup.md)
- [Further Mods to Consider](https://github.com/Enraged-Rabbit-Community/ERCFv2.5/blob/main/Documentation/Further-Mods.md)

#### Even more Happy Hare info can be found at:
- [Happy Hare Wiki](https://github.com/moggieuk/Happy-Hare/wiki)

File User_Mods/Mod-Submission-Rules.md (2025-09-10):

Before submitting a mod, make sure it follows the following mod submission rules:

### Before you submit, consider the rules

Each mod must adhere to the following rules to be eligible for User_Mods:

- Submitted mods must be compatible with ERCF v2 or v3.
- Mods must be original work by the author. When submitting the mod to this repository, the author confirms that they have not stolen this mod from another user or another website
- Mods in this repository are goverened by the repository license: [GPLv3](https://www.gnu.org/licenses/gpl-3.0.html). If you do not agree with this license, please don't submit your mod here.
- Mods must be tested, at least by the author. Ideally, more users have built and tested your mod. Join the [ERCF Discord](https://discord.com/channels/1267663557999329371/1310278996503826585) to find testers! Please don't submit untested mods.
- Mods must not represent slight modifications of existing mods/existing ERCF parts. (e.g. inconsequential addition of chamfers/fillets or other changes that don't affect the functionality of a part in a meaningful way)
- Avoid mandatory use of glue or similar assembly methods. Try to stick to the existing fastener hardware and assembly methods of ERCF and VoronDesign printers
- Mods must aim for the same standard that ERCF uses and VoronDesign applies to their printers. As such:
  - Mod files must be provided as STL/OBJ and in at least one CAD format (e.g. STEP, IGES, F3D, etc., **open formats like STEP are preferred**)
  - When submitting STLs, please try to submit them in binary format as this saves space, and allows to preview the STL files on GitHub
  - Printable mod files must be oriented in their intended printing orientation. You can use, e.g. PrusaSlicer to rotate your STLs correctly
  - Printable mod files must be printable without support. If supports are absolutely needed, they should be baked into the model as break-away supports.
  - Printable mod files must be free of errors (i.e. when importing into a Slicer, no errors should be reported)
  - Submitted mod files must not include unmodified ERCF parts
  - Submitted documents contain no sensitive data (e.g. API keys)

### Anatomy of a mod: folder structure, filenames

If you want to submit a mod and require a starting point, check out the [sample mod folder zip file](https://github.com/VoronDesign/VoronUsers/raw/main/sample_mod.zip). Simply unzip the contents over your local repository (make sure the `SAMPLE_AUTHOR` folder ends up in the `printer_mods` folder) and change folder names and contents accordingly.

In order to help users to find the appropriate files of your mod, please consider the following instructions when submitting your mod:

- To submit your mod, put it in the `User_Mods/` folder
- Create a subfolder with your name in the appropriate folder, then create further subfolders for each of your mods
- The following folder tree shows the preferred file layout of your mod. While deviations from this format can be discussed on a case-by-case basis, it is strongly encouraged to adhere to this structure to speed up the review process:
```
.
└── User_mods/
    └── Miriax/
        ├── my_mod/
        │   ├── STL/
        │   │   ├── [a]_accent_part.stl
        │   │   └── non_accent_part.stl
        │   ├── CAD/
        │   │   ├── step_file.step
        │   │   └── fusion.f3d
        │   ├── Images/
        │   │   ├── printed.jpg
        │   │   └── assembly_instructions.png
        │   ├── OTHER/
        │   │   ├── BOM.xlsx
        │   │   └── assembly_instructions.pdf
        │   ├── README.md
        │   └── .metadata.yml
        └── another_mod/
            ├── STL/
            │   └── part_1.stl
            ├── CAD/
            ├── Images/
            ├── OTHER/
            ├── README.md
            └── .metadata.yml
```
- **All filenames and foldernames in User_Mods must not have spaces in them!  Please stick to letters `a-zA-Z`, numbers `0-9`, underscores `_`, hyphens `-`, brackets `[]()` and periods `.`**
- Please keep in mind that for file and folder names, capitalization matters!  Your links and `.metadata.yml` must use the same capitalization your folders and files do.
- You can optionally indicate the color and quantity of printable parts:
  - Accent color: [a]_part_xyz.stl
  - Opaque color (Blocks light): [o]_part_xyz.stl
  - Clear/transparent color (Allows light): [c]_part_xyz.stl
  - Quantity, if more than one is needed: part_xyz_x4.stl 
- Please add a short README.md to each mod folder to provide the user with additional information, e.g. 
  - Images you provided with your mod
  - BOM for your mod (if required)
  - Assembly instructions
  - Vendor links for specific parts

Thank you for taking the time to read these rules. Head over to the [submission tutorial](How-to-Submit-to-User_Mods) to learn how you can add your mod to this repository and submit it for review.

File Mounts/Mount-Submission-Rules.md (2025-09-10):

Before submitting a mount, make sure it follows the following mount submission rules:

### Before you submit, consider the rules

Each mount must adhere to the following rules to be eligible for inclusion in Mounts:

- Submitted mounts must be compatible with ERCF v2 or v3.
- Mounts must be original work by the author. When submitting the mount to this repository, the author confirms that they have not stolen this mount from another user or another website
- Mounts in this repository are goverened by the repository license: [GPLv3](https://www.gnu.org/licenses/gpl-3.0.html). If you do not agree with this license, please don't submit your mount here.
- Mounts must be tested, at least by the author. Ideally, more users have built and tested your mount. Join the [ERCF Discord](https://discord.com/channels/1267663557999329371/1310278996503826585) to find testers! Please don't submit untested mounts.
- Mounts must not represent slight mountifications of existing mounts/existing ERCF parts. (e.g. inconsequential addition of chamfers/fillets or other changes that don't affect the functionality of a part in a meaningful way)
- Avoid mandatory use of glue or similar assembly methods. Try to stick to the existing fastener hardware and assembly methods of ERCF and VoronDesign printers
- Mounts must aim for the same standard that ERCF uses and VoronDesign applies to their printers. As such:
  - Mount files must be provided as STL/OBJ and in at least one CAD format (e.g. STEP, IGES, F3D, etc., **open formats like STEP are preferred**)
  - When submitting STLs, please try to submit them in binary format as this saves space, and allows to preview the STL files on GitHub
  - Printable mount files must be oriented in their intended printing orientation. You can use, e.g. PrusaSlicer to rotate your STLs correctly
  - Printable mount files must be printable without support. If supports are absolutely needed, they should be baked into the mountel as break-away supports.
  - Printable mount files must be free of errors (i.e. when importing into a Slicer, no errors should be reported)
  - Submitted mount files must not include unmountified ERCF parts
  - Submitted documents contain no sensitive data (e.g. API keys)

### Anatomy of a mount: folder structure, filenames

If you want to submit a mount and require a starting point, check out the [sample mount folder zip file](https://github.com/VoronDesign/VoronUsers/raw/main/sample_mount.zip). Simply unzip the contents over your local repository (make sure the `SAMPLE_AUTHOR` folder ends up in the `printer_mounts` folder) and change folder names and contents accordingly.

In order to help users to find the appropriate files of your mount, please consider the following instructions when submitting your mount:

- To submit your mount, put it in the `Mounts/` folder
- Create a subfolder with your name in the appropriate folder, then create further subfolders for each of your mounts
- The following folder tree shows the preferred file layout of your mount. While deviations from this format can be discussed on a case-by-case basis, it is strongly encouraged to adhere to this structure to speed up the review process:
```
.
└── printer_mounts/
    └── FHeilmann/
        ├── my_mount/
        │   ├── STL/
        │   │   ├── [a]_accent_part.stl
        │   │   └── non_accent_part.stl
        │   ├── CAD/
        │   │   ├── step_file.step
        │   │   └── fusion.f3d
        │   ├── Images/
        │   │   ├── printed.jpg
        │   │   └── assembly_instructions.png
        │   ├── OTHER/
        │   │   ├── BOM.xlsx
        │   │   └── assembly_instructions.pdf
        │   ├── README.md
        │   └── .metadata.yml
        └── another_mount/
            ├── STL/
            │   └── part_1.stl
            ├── CAD/
            ├── Images/
            ├── OTHER/
            ├── README.md
            └── .metadata.yml
```
- **All filenames and foldernames in Mounts must not have spaces in them!  Please stick to letters `a-zA-Z`, numbers `0-9`, underscores `_`, hyphens `-`, brackets `[]()` and periods `.`**
- Please keep in mind that for file and folder names, capitalization matters!  Your links and `.metadata.yml` must use the same capitalization your folders and files do.
- You can optionally indicate the color and quantity of printable parts:
  - Accent color: [a]_part_xyz.stl
  - Opaque color (Blocks light): [o]_part_xyz.stl
  - Clear/transparent color (Allows light): [c]_part_xyz.stl
  - Quantity, if more than one is needed: part_xyz_x4.stl 
- Please add a short README.md to each mount folder to provide the user with additional information, e.g. 
  - Images you provided with your mount
  - BOM for your mount (if required)
  - Assembly instructions
  - Vendor links for specific parts

Thank you for taking the time to read these rules. Head over to the [submission tutorial](How-to-Submit-to-Mounts) to learn how you can add your mount to this repository and submit it for review.

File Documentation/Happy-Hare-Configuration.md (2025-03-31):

#### Page Sections:
-Configuration Options for ERCFv2.5:
  - [Necessary Updates](#---necessary-configuration-updates-for-v25)
  - [Filament Cutter Options](#---filament-cutter-options)
  - [Filament Sensor Options](#---filament-sensor-options)
  - [Pregate Sensor Options](#---pregate-sensor-options)

*\[This guide was adapted from the [Happy Hare Wiki](https://github.com/moggieuk/Happy-Hare/wiki) for ERCF v2.5. Thanks Moggie!\]*

## #f03c15 #c5f015 #1589F0 Necessary Configuration Updates for v2.5

1.  Open the file `config / mmu / base / mmu.cfg`. At the top of the file, beneath `\[mcu mmu\]`, add your Local MCU's CANBus UUID. If you are using USB to connect, Happy Hare should have detected and filled your serial number in for you. If not, you must add it in at this point. Save and close the file.

2. Open the file `config / mmu / base / mmu_hardware.cfg`. If you are using a beefy NEMA17 motor for Direct Drive, you need to increase your motor currents starting on *line 128*.

The Gear Motor `run_current` should be set to *either* 70% of the motor's peak current rating, *or* the stepper driver's maximum rated current, *whichever is less.* The max for for 2209 EZ Drivers is 1.3 amps without cooling and 1.6 amps with cooling. 

If you're using the BOM motor, then set it to 1.3 amps.

3. Still in the file `config / mmu / base / mmu_hardware.cfg`. If you are using Direct Drive, comment out the Gear Ratio on line 143 by adding a hash, like this:

`#gear_ratio: 80:20			# E.g. ERCF 80:20, Tradrack 50:17`

If you are using legacy Geared Drive, you instead need the Gear Ratio to be set to match your physical gear ratio, usually 80:20 or 60:20. These numbers represent the number of teeth on the 80- or 60-tooth gears, and the 20-tooth pulley.

4. Still in the file `config / mmu / base / mmu_hardware.cfg`, on *lines 164-165*:

You want the Selector Motor `run_current` to be set to 70% of the motor's peak current rating, and the `hold_current` should be about 40% of the peak current rating.

For the BOM 1.0 amp motor, this is 0.7 amps and 0.4 amps.

Save and close the file.

## #f03c15 #c5f015 #1589F0 Filament Cutter Options

If you are using a Filament Cutter, you must update `config / mmu / base / mmu_parameters.cfg` line 334. Change the `form_tip_macro` value to `_MMU_CUT_TIP`.

> [IMPORTANT]
> If you are using a fixed cutter depressor on a gantry printer (eg Voron v2.4), there is a chance that your drag chain can catch on the depressor! You will need to create a custom Macro to wrap `_MMU_CUT_TIP` into that safely moves the toolhead into position with the depressor, like so:

```yml
[gcode_macro _MMU_SAFE_CUT_TIP]
gcode:
  G0 X50 F12000
  G0 Y305
  _MMU_CUT_TIP
  G0 X50
  G0 Y250
```

**(Do not use this without changing it! Your movement values are guaranteed to differ!)**

Instead of setting the `form_tip_macro` to `_MMU_CUT_TIP` as above, put your "safe" cutting macro with the rest of your non-MMU macros (eg. in `printer.cfg`), then set `form_tip_macro` to the name of your safe cutting macro, in this example, `_MMU_SAFE_CUT_TIP`.

Next, you will need to go through the entire file `config / mmu / base / mmu_macro_vars.cfg`. Read it, understand it, and change all of the options to suit your unique build and needs. The values you use depend on which extruder / toolhead you are using. See [Toolhead Distances](https://github.com/Enraged-Rabbit-Community/ERCFv2.5/blob/main/Documentation/Toolhead-Distances.md) for more details, but don't forget to do the hardware configuration and calibration steps first!

Critical variables to change include setting `variable_simple_tip_forming` to `False` and setting the `variable_pin_loc_xy`, but you should really *at least* review the **Movement** and **Cut Tip** sections. These control parking and tip cutting settings and variables.

## #f03c15 #c5f015 #1589F0 Filament Sensor Options

If you are using a toolhead with either an extruder sensor (before the extruder gears), a Toolhead sensor (after the Extruder gears), or both, you need to set those up.

1. Open the file `config / mmu / base / mmu_hardware.cfg`. Add the pin number(s) that your sensor(s) are connected to on lines 278-279. Save and close the file.

2. If you are using an extruder sensor specifically: Open the file `config / mmu / base / mmu_parameters.cfg`. Update the `extruder_homing_endstop` to use the value`extruder`. Save and close the file.

<!--> [!NOTE]
> If you are using a toolhead board like Nitehawk SB or the HartK ERCF toolhead board, all of the config for the toolhead board must be included *before* the MMU config, so that the MMU config can reference the pins needed!--> 

3. If you are using **both** an extruder **and** a toolhead sensor: reopen the file `config / mmu / base / mmu_parameters.cfg`. Update the `extruder_force_homing` to use the value`1`. This will ensure that during loading, the filament slows down before hitting the extruder gears, instead of crashing through them to the toolhead sensor. Save and close the file.

There are instructions for nearly-automatic calibration for almost all of the cutter and toolhead length values in the Happy Hare Wiki's [Blobbing and Stringing page](https://github.com/moggieuk/Happy-Hare/wiki/Blobbing-and-Stringing). Automatic calibration will make your life easier, you should do it.

## #f03c15 #c5f015 #1589F0 Pregate Sensor Options

Coming soon! I don't use these yet, so I need help writing this section!

### ERCF Setup Steps:
- [Flashing Your Local MCU](https://github.com/Enraged-Rabbit-Community/ERCFv2.5/blob/main/Documentation/Flashing-Local-MCU.md)
- [Installing Happy Hare](https://github.com/Enraged-Rabbit-Community/ERCFv2.5/blob/main/Documentation/Installing-Happy-Hare.md)
- Happy Hare Configuration
- [Hardware Configuration Checks](https://github.com/Enraged-Rabbit-Community/ERCFv2.5/blob/main/Documentation/Hardware-configuration-checks.md)
- [Hardware Calibration](https://github.com/Enraged-Rabbit-Community/ERCFv2.5/blob/main/Documentation/Hardware-Calibration.md)
- [Toolhead Distances](https://github.com/Enraged-Rabbit-Community/ERCFv2.5/blob/main/Documentation/Toolhead-Distances.md)
- [Installing KlipperScreen Happy Hare](https://github.com/Enraged-Rabbit-Community/ERCFv2.5/blob/main/Documentation/Installing-KlipperScreen.md)
- [Slicer Setup](https://github.com/Enraged-Rabbit-Community/ERCFv2.5/blob/main/Documentation/Slicer-Setup.md)
- [Further Mods to Consider](https://github.com/Enraged-Rabbit-Community/ERCFv2.5/blob/main/Documentation/Further-Mods.md)

#### Even more Happy Hare info can be found at:
- [Happy Hare Wiki](https://github.com/moggieuk/Happy-Hare/wiki)

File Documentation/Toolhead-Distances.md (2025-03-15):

#### Page Sections:
- [Correct Meaning of Key Dimensions](#---correct-meaning-of-key-dimensions)
- [Calibrating Toolhead](#---calibrating-toolhead)
  - [Final Blob Tuning](#---final-blob-tuning---toolhead_ooze_reduction)
  - [Toolchange Retraction](#---tool-change-retraction)
  - [Z-Hop and Ramping](#---z-hop-and-ramping)
- [Summary of Tuning Steps](#---summary-of-tuning-steps)
- [Cleaning Extruder with Cold Pull](#---cleaning-extruder-with-a-cold-pull)

<br>

This discussion assumes that you have initial setup complete and are now ready to tune the quality of your prints. Although some of the information contained here is useful early in your journey it will make a lot more sense once you have some experience with default or "borrowed" toolhead parameters. You *must* configure and calibrate your hardware before doing this step.

This guide will then guide you to optimize a few critical parameters for print quality that avoids blobbing on your wipetower or print and stringing when moving to change tool.

Specifically in this guide you will learn how to correctly set the following parameters (`mmu/base/mmu_parameters.cfg`):
- `toolhead_extruder_to_nozzle`
- `toolhead_sensor_to_nozzle`
- `toolhead_entry_to_extruder`
- `toolhead_residual_filament`
- `toolhead_ooze_reduction`

It will also illustrate how to use z-hop movement/ramping and retraction settings to eliminate blobs and stringing during color changes or EndlessSpool operations in your prints (`mmu/base/mmu_macro_vars.cfg`):
- `variable_park_toolchange`, `variable_park_mmu_error`, `variable_park_pause`, `variable_park_cancel`, `variable_park_complete`
- `variable_restore_xy_pos`
- `variable_park_travel_speed`, `variable_park_lift_speed`
- `variable_retract`, `variable_retract_speed`, `variable_unretract_speed`

And finally, set key tip cutting macro variables (`mmu/base/mmu_macros_vars.cfg`):
- `variable_blade_pos`
- `variable_retract_length`

<br>

## #f03c15 #c5f015 #1589F0 Correct Meaning of Key Dimensions

Firstly it is important to understand that while sensors like a toolhead sensor can help with extruder loading and unloading, the process relies on precise movement distances. These "dimensions" often interact with each other so it is also important that they are set correctly and match the meaning Happy Hare is expecting. Doing so will give deterministic toolchanges rather than a "these settings seem to work" scenario.

When the extruder is loaded, Happy Hare will move the filament a precise distance from either the extruder gear or the toolhead sensor to the end of the nozzle. This distance is set with `toolhead_extruder_to_nozzle` and/or `toolhead_sensor_to_nozzle` and represents the CAD measured distance in a perfectly clean extruder/nozzle. The reality is that once the extruder is "dirty" this distance changes. This is because some filament is inevitably left behind in the extruder/nozzle shortening this distance. The amount of filament remaining seems to vary greatly from a couple of mm to as much as 15mm in some high flow hotends! In addition, CHT type nozzles use an insert that is not accounted for in external toolhead measurements and often neither in CAD, which equally effects the accuraacy of these measurements. 

To account for this, Happy Hare defines `toolhead_extruder_to_nozzle` and `toolhead_sensor_to_nozzle` as theoretical and thus should be able to be pulled form CAD drawings or other users. It uses `toolhead_residual_filament` to represent how much to reduce the loading move by for the new filament to butt up against the old without accidently blobbing.

In practice it has been hard to determine these values other than through experimentation and even then it is hard to determine for example, whether to increase `toolhead_residual_filament` or reduce `toolhead_sensor_to_nozzle`.

Let's run through the important steps in a toolchange (for both tip forming and tip cutting cases) and relate to these parameters:

### With Tip Forming

Transitioning from an orange filament to a blue _(Click on images to see the detail)_:

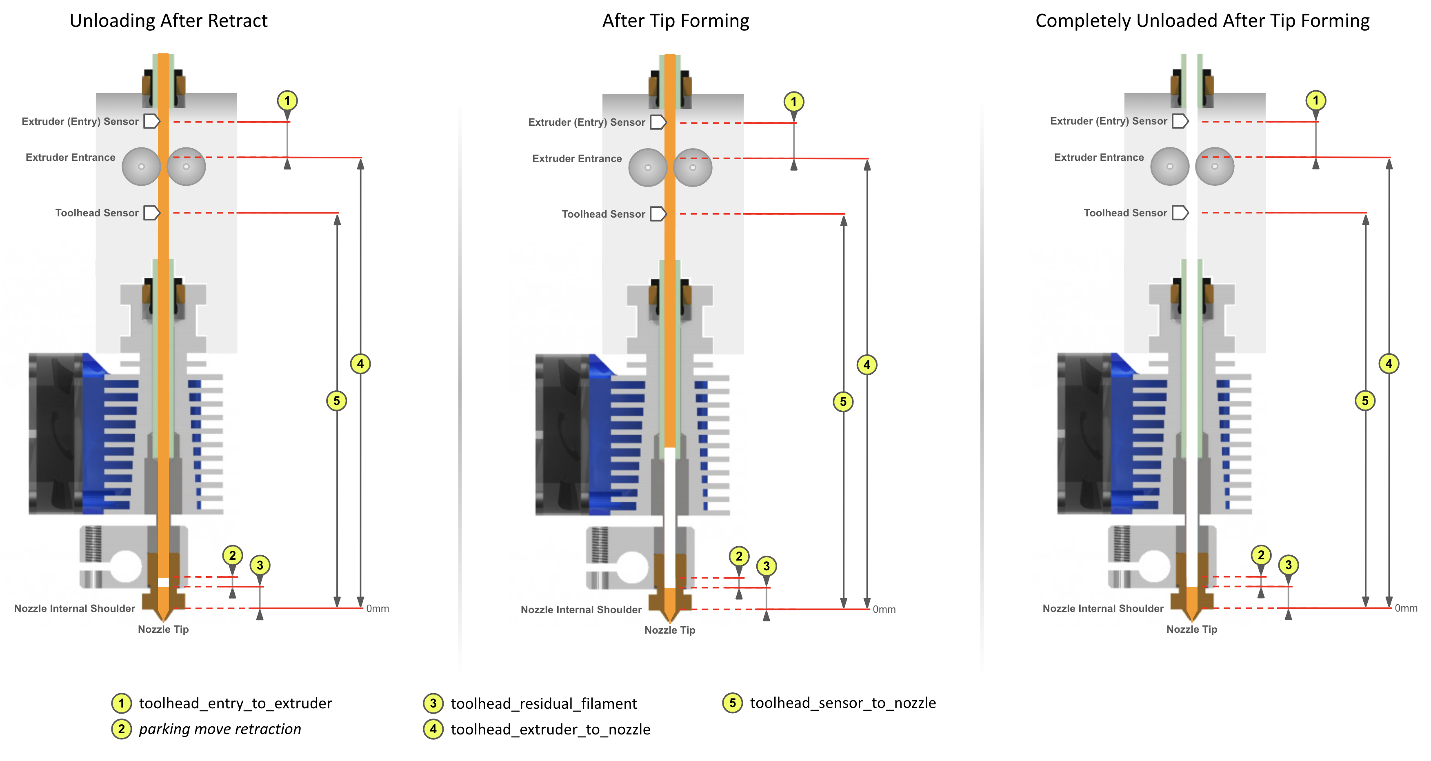
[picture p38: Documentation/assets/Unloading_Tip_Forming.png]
Unloading Tip Forming
<p align="center"></p>
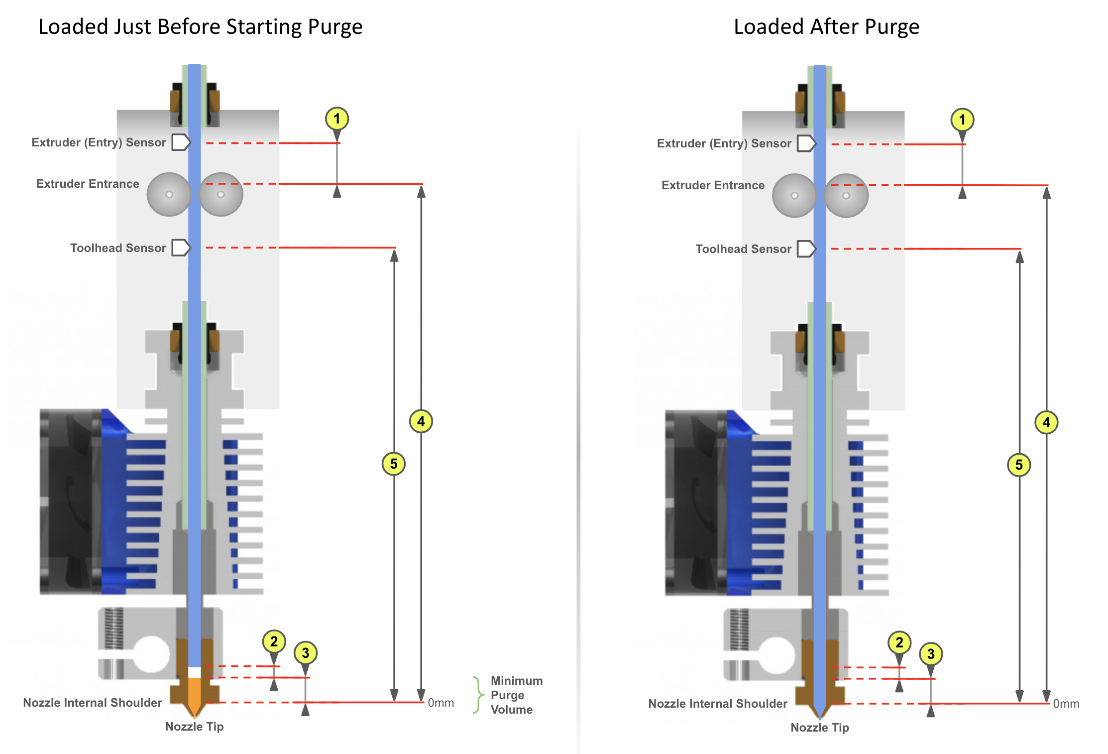
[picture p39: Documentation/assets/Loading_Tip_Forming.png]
Loading Tip Forming
<p align="center"></p>

<br>

### With Toolhead Tip Cutting

With toolhead tip cutting the procedure is a little more complex and introduces two additional macro variables (defined in `mmu_macro_vars.cfg` that configure the tip cutting logic):

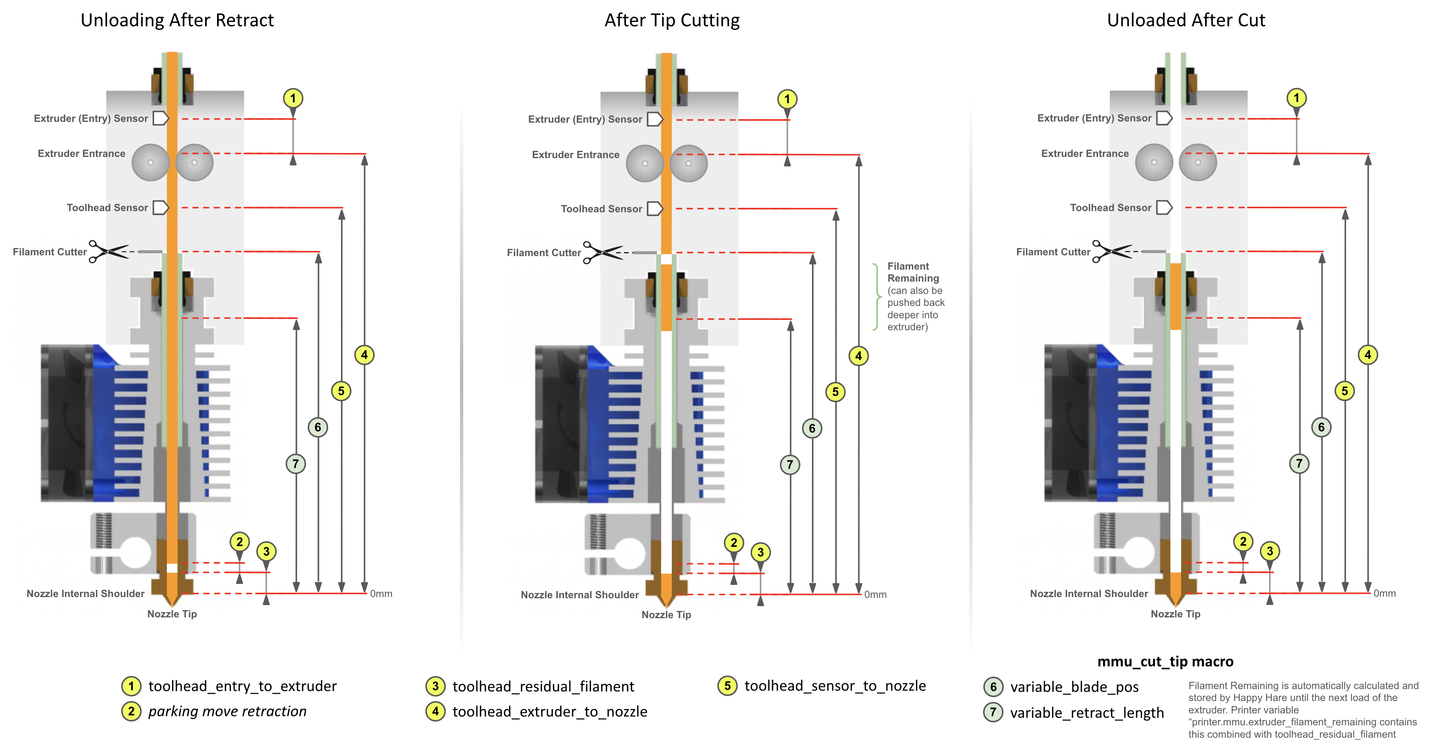
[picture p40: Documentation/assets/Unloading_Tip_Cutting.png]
Unloading Tip Cutting
<p align="center"></p>
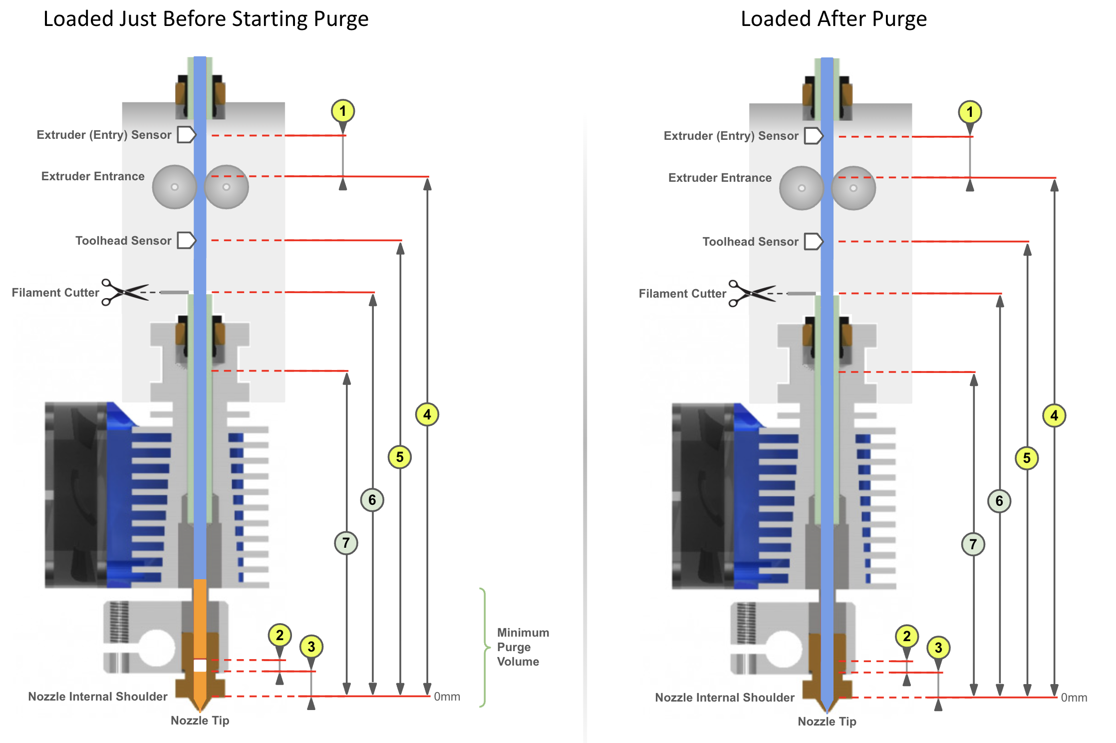
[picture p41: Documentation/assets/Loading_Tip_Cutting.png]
Loading Tip Cutting
<p align="center"></p>

Note that the cut piece of filament remaining and the residual filament are automatically accounted for by Happy Hare so long as you have configured the parameters exactly as defined in this illustration.

> [!TIP] 
> The printer variable `printer.mmu.extruder_filament_remaining` contains the total length of filament left in the extruder combining both the `toolhead_residual_filament` and length of any cut tip.<br>
> Related is the printer variable `printer.mmu.toolchange_purge_volume` that calculates the total volume of filament to be purged by summing both the slicer tool map purge volume and the volume of this remaining material.

<br>

> [!IMPORTANT]  
> 1. The really important reference point is the internal nozzle "shoulder". This is considered the 0mm reference point for most parameters. For CHT nozzle this will be further away from the tip than regular nozzles.
> 2. You can see how the `toolhead_XXX_to_nozzle` settings and `toolhead_residual_filament` are related, so while you can tune the former and ignore latter, it is recommended you use them correctly so that Happy Hare is able to control the filament movement when loading and unloading the toolhead and correctly influence purge volumes.
> 3. `toolhead_residual_filament` is dependent on your extruder and nozzle. High flow and CHT systems generally have a much higher value i.e. more residual filament left over in the extruder) than regular ones.

<br>

## #f03c15 #c5f015 #1589F0 Calibrating Toolhead

Ok, now you know what the correct meaning of the dimensions are the next question is how to discover them for your setup. For everything other than `toolhead_residual_filament` it is possible to use accurate CAD models to measure them (remember to use the internal shoulder in the nozzle). This can be a challenge if using a CHT nozzle as shown below.

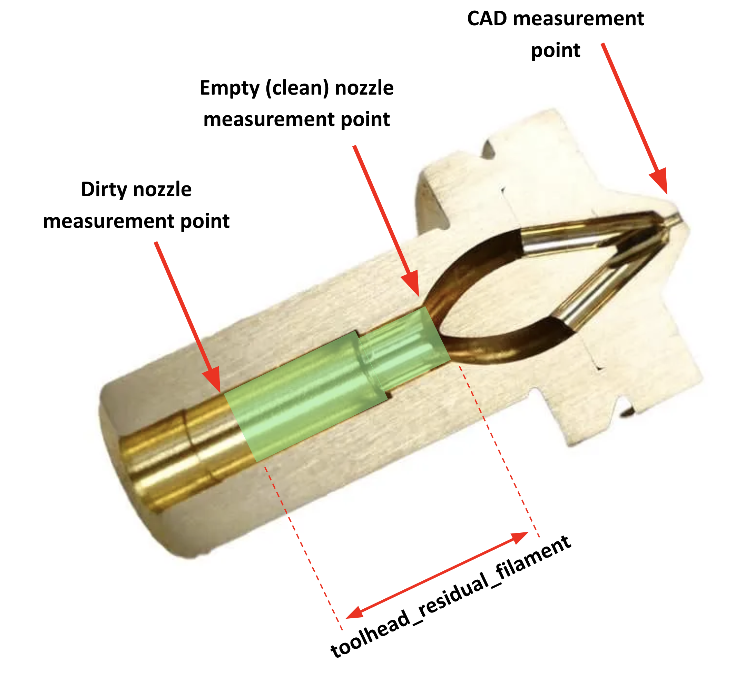
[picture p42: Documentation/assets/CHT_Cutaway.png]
CHT Cutaway
<p align="center"></p>

If you have a toolhead sensor there is now an automated way to measure! If not, then you can refer to this wiki in the future, where we will aim to collate verified measurements for common toolhead combinations and once you have those set, you can experiment to discover the correct `toolhead_residual_filament` setting.

If you have a toolhead sensor continue reading below.

Now Happy Hare can help with a new `MMU_CALIBRATE_TOOLHEAD` command.

<br>

### ✅ Step 1: Perform a cold pull to empty your nozzle

This process requires you to start with a CLEAN (as in empty) extruder and nozzle. To do this you need to perform a cold pull. During this operation, you warm up the extruder, purge some filament, then let the nozzle cool. At the right temperature and using a bit of force you manually pull the filament out pulling with it all the old residue as well as any carbon deposits. This is something that most of you probably already know how to do, but for those that need help, or want a more convenient way to perform it you can run the supplied `MMU_COLD_PULL` macro and follow the directions displayed in the console. This is documented [later in this page](#---cleaning-extruder-with-a-cold-pull).

<br>

### ✅ Step 2: Calibrate the empty toolhead dimensions

If you have removed the Bowden tube, reattach it to the toolhead, and prepare the MMU bu selecting the gate you with to use. Ensure filament is available and parked at the gate but don't load the extruder yet.

Then run:

> MMU\_CALIBRATE\_TOOLHEAD CLEAN=1

(optionally add `SAVE=0`)

This will perform a number of probing moves with a cold extruder and report back the empty toolhead parameters. For example:

```
Reminder:
1) 'CLEAN=1' with clean extruder for: toolhead_extruder_to_nozzle, toolhead_sensor_to_nozzle (and toolhead_entry_to_extruder)
2) No flags with dirty extruder (no cut tip) for: toolhead_residual_filament (and toolhead_entry_to_extruder)
3) 'CUT=1' holding blade in for: variable_blade_pos
Desired gate should be selected but the filament unloaded

Modifying MMU gear stepper run current to 40% for collision detection
Run Current: 0.21A Hold Current: 0.09A
Restoring MMU gear stepper run current to 100% configured
Run Current: 0.49A Hold Current: 0.09A
Measuring clean toolhead dimensions after cold pull...
Measured toolhead_sensor_to_nozzle: 62.1
Measured toolhead_extruder_to_nozzle: 70.6
Measured toolhead_entry_to_extruder: 7.9
-----------------------------------
Calibration Results (clean nozzle):
> toolhead_extruder_to_nozzle: 70.6 (currently: 70.0)
> toolhead_sensor_to_nozzle: 62.1 (currently: 62.0)
> toolhead_entry_to_extruder: 7.9 (currently: 8.5)
-----------------------------------
New toolhead calibration active until restart. Update mmu_parameters.cfg to persist settings
```

Assuming you didn't run with the `SAVE=0` option this will temporarily adjust your toolhead parameters, but it will not save them in the configuration files.

> [!TIP]  
> 1. You must note these down and manually update `mmu_parameters.cfg` for them to persist across a restart. Do this once you have finished the complete calibration guide on this page.
> 2. If you want to validate your results, you can run the process again before the next step. You can add the `SAVE=0` parameter to skip updating those variables. Just be mindful that the filament will grind a little in the gears and extruder, so make sure you eject the filament fully from you MMU, cut the used portion and try with a new filament segment again.
> 3. If you have a filament tension/compression sensor like Belay installed on your bowden path, make sure you "lock" it in place so it doesn't move. It is important that the filament path length stays static throughout the calibration process. You can either remove it and install a coupler or simply hold it firmely in its fully extended position when the calibration commands are run.

<table>
<tr>
<td>

Because the extruder was empty we were able to establish the position of the internal nozzle shoulder as well (almost magically) the `toolhead_extruder_to_nozzle`, `toolhead_sensor_nozzle` and `toolhead_entry_to_extruder` distances.

</td>
<td width=30%>
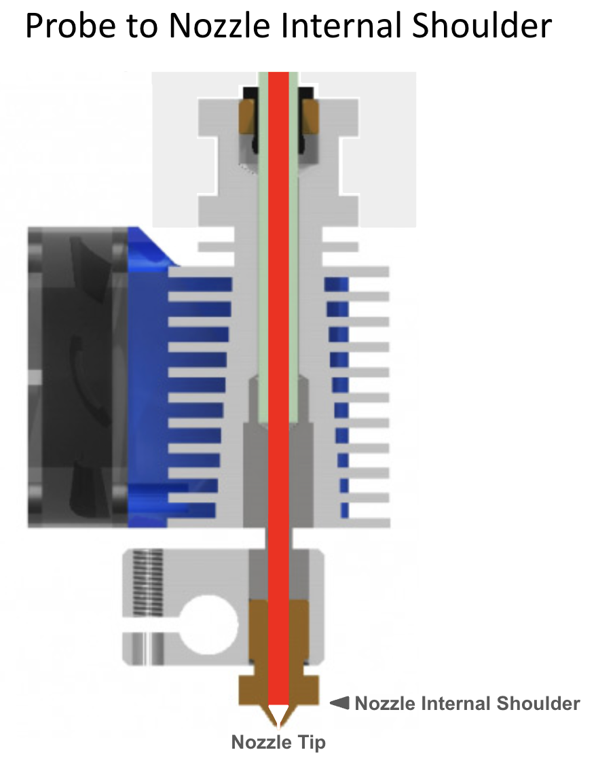
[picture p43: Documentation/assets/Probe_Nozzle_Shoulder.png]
Probe Nozzle Shoulder

</td>
</tr>
</table>

<br>

### ✅ Step 3: Load (dirty) the nozzle with filament

During this operation we will load filament all the way to the end of the nozzle tip and extrude some. We will then unload the extruder simulating the amount of molten filament that will be left over inside the nozzle tip when filament is ejected.

As the previous step may have ground your filament a little, make sure you unload your filament from the MMU, remove it, cut any used parts and re-insert at the gate. This will ensure you start this step with a fresh piece of the same filament, improving the accuracy of your results.

#### If you are using tip forming:

Heat up your extruder to your filament print temperature , and run the load and unload filament macros as below:
1. `MMU_LOAD` or `Tx`
2. Manually extrude some filament using the printer’s web interface
3. `MMU_UNLOAD`
4. Switch off your nozzle heater (set the nozzle temperature to 0°C)

#### If you are using tip cutting:
As the tip cutting operation would normally leave additional filament in the toolhead that we don’t want, the dirtying of the extruder is slightly different to the above and avoids the actual cutting action:
1. `MMU_LOAD` or `Tx`
2. Manually extrude some filament using the printer’s web interface
3. `MMU_UNLOAD SKIP_TIP=1` (notice the option)
5. Switch off your nozzle heater (set the nozzle temperature to 0°C)

<br>

### ✅ Step 4: Calibrate residual filament (with dirty nozzle)

Now that the nozzle is “dirty” and simulating the left over material after a filament ejection, it is time to calibrate the residual filament parameter.

To do this, run the below command, with no arguments.

> MMU\_CALIBRATE\_TOOLHEAD
```
...blah blah blah...
-----------------------------------
Calibration Results (dirty nozzle):
> toolhead_residual_filament: 3.0 (currently: 3.4)
-----------------------------------
New calibrated ooze reduction active until restart. Update mmu_parameters.cfg to persist
```

> [!TIP]  
> 1. You can run a dirty calibration as often as you like and to see if it differs with different filament types, changes you make to your tip forming macro, etc.
> 2. Just be mindful that filament will grind a little in the gears & the extruder, so make sure you eject the filament fully from your MMU, cut the used portion and try with a new filament segment again.
> 3. If you are curious, you can also use it as a trick way to measure the "filament_remaining" after tip cutting, validating that you are not cutting molten filament. Just remember to use the SAVE=0 option because you DON'T want to `toolhead_residual_filament` to include the cut piece of filament!
> 4. Again you can use the optional command SAVE=0 to skip saving the results in memory. 
> 5. If you don’t have a filament cutter, the calibration process is done. Make sure you note down the above measurements and update them together with the ones from the first step in your `mmu_parameters.cfg` file. If you do have a filament cutter, make sure you follow step 4 below.  
> 6. If you have a belay sensor (filament tension/compression sensor) installed on your Bowden path, make sure you “lock” it in place so it doesn’t move. It is important that the filament path length stays static throughout the calibration process. You can either remove it and install a coupler or simply hold it firmly in its fully extended position when the calibration commands are run.

> [!IMPORTANT] 
> Remember, that the calibrated `toolhead_residual_filament` is your starting point. You can still fine tune the reduction in loading length according to what you see happening with the wipetower with and actual print. See [Tip Forming and Purging](https://github.com/moggieuk/Happy-Hare/wiki/Tip-Forming-and-Purging#tuning-toolhead_ooze_reduction) for details on what to look for and how to use `toolhead_ooze_reduction` as the final parameter to tweak load volume. But a word of warning, this should be the very last step and should only be a very small adjustment to optimize blobbing and oozing during tool loading.

<table>
<tr>
<td>

Again referring back to the earlier illustrations, the difference between the clean reading and the dirty one is what `toolhead_residual_filament` compensates for and represents the residual filament that is always left behind in the extruder. The command will also measure the `toolhead_entry_to_extruder` variable but these should be similar (as in less than 1mm difference) between the two runs. If this is substantially different, you can re-run the calibration routine as the measurement was probably not accurate enough the first time.

</td>
<td width=30%>
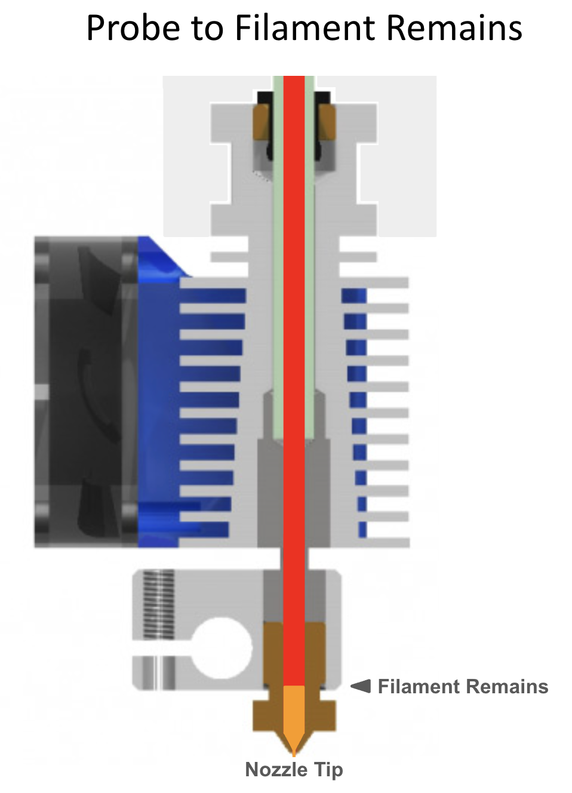
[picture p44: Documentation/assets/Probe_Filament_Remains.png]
Probe Filament Remains

</td>
</tr>
</table>

<br>

### ✅ Step 5: Calibrate toolhead cutting macro variables (if using a filament cutter)

If you have a toolhead cutter, you must now calibrate the blade cutting position `variable_blade_pos` and set the `variable_retract_length`. Because the other toolhead dimensions are now different from your original settings, the blade position will most likely also need to be calibrated correctly. 

These variables control the amount of cut filament left in the extruder after the cut operation, so they need to be correct to avoid oozing when loading the toolhead after a cut move.

To calibrate the above:
1. Run `MMU_LOAD` or `Tx` to load filament in your extruder
2. Switch off the nozzle heating element (set nozzle temperature to 0) and wait for it to cool down.
3. Manually press the cut lever a couple of times to ensure the filament is cleanly cut. 
4. After you have cut the filament, unload/eject without further tip forming by running `MMU_UNLOAD SKIP_TIP=1` (did you notice the skip tip option?)
5. With the filament unloaded and parked in the MMU and a cold nozzle, run `MMU_CALIBRATE_TOOLHEAD CUT=1`

> [!TIP]  
> TIME SAVER: Rather than loading, cutting and cooling you can simply (with the extruder unloaded) press and HOLD the cutter blade in the closed postion. STAY in this position until the calibration is complete. Note that the measurement will be shorter by one blade thickness, so add 0.5mm to the reported distance.

> MMU\_CALIBRATE\_TOOLHEAD CUT=1
```
...blah blah blah...
-----------------------------------
Calibration Results (cut tip):
> variable_blade_pos: 36.2 (currently: 37.5)
> variable_retract_length: 5.0-36.2, recommend: 32.2 (currently: 32.5)
-----------------------------------
New calibrated variables active until restart. Update mmu_macro_vars.cfg to persist
```

> [!TIP]  
> The larger the `variable_retract_length` the less additional purge is necessary to clean out the prior color. However, if you get too aggressive you may experience clogs because you are cutting a hot part of the filament. Experience has shown that about 5mm shorter than the blade position (i.e. 5mm cut length) is about as good as you can get. If you do still run into clogging issues, shorten the `variable_retract_length` value.

Again if you are using a filament tension/compression sensor, make sure you lock it in place for the duration of the calibration moves.

<table>
<tr>
<td>

Referencing earlier illustrations, the blade position `variable_blade_pos` can thus be established and a range of sensible values for `variable_retract_length` is recommended.

</td>
<td width=30%>
<a href="https://github.com/Enraged-Rabbit-Community/ERCFv2.5/blob/main/Documentation/assets/Probe_Cut_Remains.png">Probe Cut Remains</a>
</td>
</tr>
</table>

<br>

### Summary of MMU\_CALIBRATE\_TOOLHEAD options

  | Order | Option | Description |
  | ----- |------ | ----------- |
  | 1 | `CLEAN=1` | This will calibrate `toolhead_extruder_to_nozzle`, `toolhead_sensor_to_nozzle`, `toolhead_entry_to_extruder` and MUST be run on clean extruder after cold-pull | 
  | 2 | _none_ | This will calibrate `toolhead_residual_filament` and should be run with a dirty extruder where tip has been formed for filament retracted from extruder. It must not be run after tip cutting |
  | 3 | `CUT=1` | This will calibrate `variable_blade_pos` and suggest `variable_retract_length` for the tip cutting macro. This MUST be run after loading the extruder and manually cutting the filament and running `MMU_UNLOAD SKIP_TIP=1` to unload without re-running the tip cutting macro |

<br>

With the toolhead now properly configured you should experience better basic loading and uploading with reduction of blobbing and thus stringing. However, there is more... 

<br>

## #f03c15 #c5f015 #1589F0 Final blob tuning - `toolhead_ooze_reduction`

Incorrect toolhead dimensions contribute most to blobbing problems, but even when perfect, blobbing can still occur when the toolhead is loaded. The reason might be air pockets or similar in the extruder or a slight variation in the `toolhead_residual_filament`. Therefore once the toolhead is properly calibrated (with likely fixed values), there is one tuning parameter left. 

This parameter `toolhead_ooze_reduction` should start with a value of 0. It can be tuned to further reduce the extruder loading length to completely eliminate blobs on the wipetower. A positive value will DECREASE the load length by that number of mm. Typically a few mm is all that is required and if you find yourself needing more, check your `toolhead_residual_filament` value. Technically this value can be slightly negative - the effect would be to INCREASE the loading length.

The best way to tune this is while actually printing (it can be altered dynamically during a print with `MMU_TEST_CONFIG`). Refer to this [Tip Forming and Purging](https://github.com/moggieuk/Happy-Hare/wiki/Tip-Forming-and-Purging#tuning-toolhead_ooze_reduction) page for more details.

<br>

## #f03c15 #c5f015 #1589F0 Tool change retraction

Just like when printing, it is usually necessary to relax the pressure in the extruder prior to a travel move to prevent the slow oozing that would otherwise occur. 

This is where the `retraction` setting comes in. It is set to the filament retraction distance that will be applied immediately before the z-hop move and any travel movements during the toolchange. All the supplied macros will understand this setting and compensate for this accordingly. Generally 2-3mm of retraction will minimize oozing although it might be a little higher on high flow systems.

At the end of the toolchange process and immediately following the reversal of the z-hop move, the un-retract will occur to correctly pressurise the extruder again. In this manner the extruder is never fully loaded during travel moves and thus oozing is minimized.

The retraction and un-retraction speed is set with the related `variable_retract_speed` and `variable_unretract_speed` variables and can thus be set independently (often faster) than your general extruder load/unload speeds.

> [!NOTE]  
> The retraction settings are configured in the MOVEMENT section of `mmu_macro_vars.cfg` and can be specified independently for different operations including toolchange, print complete, pause, cancel, etc. See this section in [Toolchange Movement](https://github.com/moggieuk/Happy-Hare/wiki/Toolchange-Movement#---overview-of-toolhead-parking-movement) for more details.

<br>

## #f03c15 #c5f015 #1589F0 Z-Hop and Ramping

When a toolchange occurs, it is preferable to move the toolhead away from the print so the hot nozzle isn't left on the print causing marks. 

However, such travel moves can graze the top of the print. This is mitigated by performing a z-hop move (i.e. raising the toolhead) before travelling. The height of the z-hop move is controlled by the `z_hop` parameter in the toolhead parking and movement section of `mmu_macro_vars.cfg`. It is performed immediately after the toolchange retraction (also specified in the same parking and movement section), with usually 1mm being plenty to stay clear of the print.

Despite the retraction and upward movement many filaments will still have a tendency to "string" because a straight up retraction move pulls viscous filament from the nozzle. 

To minimize stringing during the zhop move, what is needed is a much larger toolhead movement in the XY plane to "break the strings". This is controlled by the `z_hop_ramp` setting, which is the length of the horizontal move performed together with the vertical z hop move (`z_hop_height`). 

This ramped z-hop move essentially allows for a fast travel move of a greater distance than vertical movements which are generally much slower and shorter than horizontal. 

To ensure the toolhead does not go out of the print plate “bounds”, the horizontal movement component will be performed towards the center of the build plate.

For full details on how to setup parking and thus define z-hop and retraction movements, read [Toolchange Movement](https://github.com/moggieuk/Happy-Hare/wiki/Toolchange-Movement) page.

<br>

## #f03c15 #c5f015 #1589F0 Summary of Tuning Steps

Proceed in this order:<br>
1. MMU_CALIBRATE_TOOLHEAD settings are defined in `mmu_parameters.cfg`
2. toolhead_ooze_reduction is defined in `mmu_parameters.cfg`
3. PARKING_MOVEMENT_SETUP is defined in MOVEMENT section of `mmu_macro_vars.cfg`

```mermaid
stateDiagram-v2
    MMU_Operational --> MMU_CALIBRATE_TOOLHEAD
    state MMU_CALIBRATE_TOOLHEAD { 
        direction LR
        toolhead_XXX_to_nozzle --> toolhead_entry_to_extruder
        toolhead_entry_to_extruder --> toolhead_residual_filament
    }
    MMU_CALIBRATE_TOOLHEAD --> toolhead_ooze_reduction
    toolhead_ooze_reduction --> PARKING_MOVEMENT_SETUP
    state PARKING_MOVEMENT_SETUP {
        direction LR
        retraction --> z_hop
        z_hop --> z_hop_ramp
    }
```

<br>

## #f03c15 #c5f015 #1589F0 Cleaning Extruder with a "Cold-Pull"

The cold pull method to clean your extruder is one of the most useful things to be in your bag of printer maintenance tricks! 

Generally, it is a great way to clean carbon deposits that build up over time and can result in under extrusion or dark spots in your prints. 

For this guide, we are using it to empty the nozzle and prepare it for accurate toolhead dimension measurements. However, feel free to use it as part of your periodic nozzle cleaning too!

### Manual Cold Pull Procedure
1. Move toolhead to a convenient location, often the front middle of your build plate and at least 20mm above
2. Detach the Bowden tube from the toolhead
3. Open the extruder latch and manually load a 250mm piece of filament all the way in to the nozzle. Then close the extruder latch.
4. Extrude at least 20mm-30mm of filament or until it comes out the same color as your loaded filament.
5. Turn of the nozzle heater and wait for the nozzle to cool down
6. Keep the nozzle completely full by occasionally extruding 1-2mm of filament while the nozzle is still reasonably hot for your filament
7. Heat the extruder back to the cold pull temperature
8. At this point, pull the filament quite firmly and evenly out of the extruder in a vertical direction
9. Inspect the tip to see if it has been successful

### Using MMU\_COLD\_PULL macro
To help with the process Happy Hare includes a special macro that will guide you through the process and can also run it for you in a fully automated manner. To run it:

1. Move the toolhead to a convenient location, often the front middle of your build plate and at least 20mm above
2. Detach the bowden tube from toolhead
3. Open the extruder latch and manually load a 250mm piece of filament all the way in to the nozzle. Then close the extruder latch.
4. Run `MMU_COLD_PULL MATERIAL=nylon|pla|abs|petg`. Optionally you can add temperature overrides e.g. `PULL_TEMP=xxx` (see [Command Reference](https://github.com/moggieuk/Happy-Hare/wiki/Command-Reference#---calibration) for details) to better suite your material (see [table of defaults](#default-mmu_cold_pull-temperatures-for-different-materials) below)
5. Be ready to pull at the right time! You will be given a little warning but it is important to pull at the correct temperature when the filament is still slightly pliable. 
6. Pull directly upwards with a consistent firm pull. The extruder stepper will also spin to aid the pull. If you want to do the pull manually, unlatch the extruder and pull. Note: some extruders (like the Galileo 2) have enough grip and torque to do this without assistance, although the manual approach allows you to "feel" the correct pull speed.

> MMU\_COLD\_PULL MATERIAL=pla
```yml
Cold Pull with pull_temp=120°C, hot_temp=250°C, min_extrude_temp=160°C, cold_temp=45°C
Heating extruder to 250°C
Cleaning nozzle tip with 25mm of filament
Allowing extruder to cool...
Stuffing nozzle at 250°C
Stuffing nozzle at 240°C
Stuffing nozzle at 230°C
Stuffing nozzle at 220°C
Stuffing nozzle at 210°C
Stuffing nozzle at 200°C
Stuffing nozzle at 190°C
Stuffing nozzle at 180°C
Stuffing nozzle at 170°C
Waiting for extruder to completely cool to 45°C...
Nozzle at 150°C
Nozzle at 140°C
Nozzle at 130°C
Nozzle at 120°C
Nozzle at 110°C
Nozzle at 100°C
Nozzle at 90°C
Nozzle at 80°C
Nozzle at 70°C
Nozzle at 60°C
Nozzle at 50°C
Re-warming extruder to 100°C
Get ready to pull...
>>>>> PULL NOW <<<<<
Cold pull is successful if you can see the shape of the nozzle at the filament end
```

**How do you know if the cold pull was successful?** The pulled end of the filament should like one of the pictures below. You need to be able to see the impression of the nozzle at the tip of the pulled filament. On regular nozzles it should look similar to the image on the left, while with CHT nozzles similar to the image on the right. Note that the author of that picture (@igiannakas) should be commended for an excellent result because CHT nozzles require the pull at exactly the right temperature and a bit of luck!

<p align="center">Cold Pull Normal Cold Pull Normal</p>

It may take a few pulls to get suitable results...

> [!TIP]  
> - Some materials are better than others for cleaning with nylon often being found to be the best. PLA is also good. PTEG and ABS can be used but often stretch and snap rather than pulling with sufficient force. The cold pulling temperature will be different with each material type so you may need to experiment.
> - You may need to repeat the process if the purpose is to completely clean your nozzle of carbon rather than just prepare for calibration
> - Feedback is that clear filament may be the strongest. Avoid filaments with strong pigmentation.

### Default `MMU_COLD_PULL` temperatures for different materials

 | Material | hot_temp | cold_temp | pull_temp | min_extrude_temp | Suitability |
 | -------- | -------- | --------- | --------- | ---------------- | ----------- |
 | NYLON    | 260      | 50        | 120       | 190              | Best        |
 | PLA      | 250      | 42        | 100       | 160              | Good        |
 | ABS      | 255      | 50        | 120       | 190              | Ok          |
 | PETG     | 250      | 42        | 100       | 180              | Ok          |

The `min_extrude_temp` is the temperature above which `MMU_COLD_PULL` will keep the nozzle pressurised with filament to ensure it is completely full.

Good luck!

### ERCF Setup Steps:
- [Flashing Your Local MCU](https://github.com/Enraged-Rabbit-Community/ERCFv2.5/blob/main/Documentation/Flashing-Local-MCU.md)
- [Installing Happy Hare](https://github.com/Enraged-Rabbit-Community/ERCFv2.5/blob/main/Documentation/Installing-Happy-Hare.md)
- [Happy Hare Configuration](https://github.com/Enraged-Rabbit-Community/ERCFv2.5/blob/main/Documentation/Happy-Hare-Configuration.md)
- [Hardware Configuration Checks](https://github.com/Enraged-Rabbit-Community/ERCFv2.5/blob/main/Documentation/Hardware-configuration-checks.md)
- [Hardware Calibration](https://github.com/Enraged-Rabbit-Community/ERCFv2.5/blob/main/Documentation/Hardware-Calibration.md)
- Toolhead Distances
- [Installing KlipperScreen Happy Hare](https://github.com/Enraged-Rabbit-Community/ERCFv2.5/blob/main/Documentation/Installing-KlipperScreen.md)
- [Slicer Setup](https://github.com/Enraged-Rabbit-Community/ERCFv2.5/blob/main/Documentation/Slicer-Setup.md)
- [Further Mods to Consider](https://github.com/Enraged-Rabbit-Community/ERCFv2.5/blob/main/Documentation/Further-Mods.md)

#### Even more Happy Hare info can be found at:
- [Happy Hare Wiki](https://github.com/moggieuk/Happy-Hare/wiki)

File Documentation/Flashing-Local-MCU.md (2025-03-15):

*These instructions were copied from the manuals provided by BTT, FysEtc, and Tircown and updated for ERCF v2.5.*

> [!IMPORTANT] 
> These instructions assume you already have CAN communication working on your printer (unless you're using a USB connection). If you don't, check out [Esoterical's CANBus Guide](https://canbus.esoterical.online/).

**Click on the relevant headings for your mainboard:**

<details>
<summary>Flashing Katapult onto MMBv1.1</summary>

> **NOTE**
> Katapult (formerly CanBoot) is for updating MCU firmware directly via CAN Bus. If you prefer to update your firmware via USB (DFU Mode), skip this entire section.

To flash Katapult onto Raspberry Pi or CB1, refer to the following instructions to download the Katapult project: https://github.com/Arksine/katapult

1. Connect to CB1/Raspberry Pi via SSH and enter the command `cd ~` to go to the home directory.
Use the command `git clone https://github.com/Arksine/katapult` to download the Katapult project. Then enter `cd katapult` to navigate to the Katapult directory.

2. Enter `make menuconfig` and configure as shown in the provided image:

Katapult Firmware Options

3. Use the command `make` to compile the firmware. The resulting katapult.bin file will be in the home/username/katapult/out folder. This can be directly downloaded to your computer from the SSH software's left panel.

Katapult binary download

4. Hold the Boot button and connect the board to Raspberry Pi/CB1 via Type-C cable to enter DFU mode.

5. Enter `lsusb` in the SSH terminal to query the DFU device ID.

Querying DFU devide ID

6. Enter the following command to flash Katapult: `make flash FLASH_DEVICE=0483:df11`

> **NOTE**
> Replace `0483:df11` with the actual device ID found in the previous step.

7. After flashing, disconnect the Type-C cable.
</details>

---

<details>
<summary>Compiling Klipper Firmware for MMBv1.1</summary>

1. Connect to CB1/Raspberry Pi via SSH and enter the following commands:
`cd ~/klipper/`
`make menuconfig`

Configure the firmware as shown in the provided image (update Klipper firmware to the latest version if options are not available).

Querying DFU devide ID

`[*] Enable extra low-level configuration optionsMicro-controller`

`Micro-controller Architecture (STMicroelectronics STM32) --->`

`Processor model (STM32G0B1) --->`

If not using Katapult:

`Bootloader offset (No bootloader) --->`

If using Katapult:

`Bootloader offset (8KiB bootloader) --->`

If USB communication on Type-C is used:

`Communication interface (USB (on PA11/PA12)) --->`

If CAN-Bus communication is used:

`Communication interface (CAN bus (on PB0/PB1)) --->`
`(1000000) CAN bus speed`

2. After configuration, press `q` to exit, and select `Yes` when prompted to save.

3. Enter `make` to compile the firmware. The resulting `klipper.bin` file will be in the `home/username/klipper/out` folder. This can be directly downloaded to your computer from the SSH software's left panel.

Klipper binary download

</details>

---

<details>
<summary>Flashing Katapult onto MMBv2.0</summary>

> **NOTE** 
> Katapult (formerly CanBoot) is for updating MCU firmware directly via CAN bus. If you prefer to update via USB (DFU Mode), skip this entire section.

To flash Katapult onto Raspberry Pi or CB1, refer to the following instructions to download the Katapult project: https://github.com/Arksine/katapult

1. Connect to CB1/Raspberry Pi via SSH and enter the command `cd ~` to go to the home directory.
Use the command `git clone https://github.com/Arksine/katapult` to download the Katapult project. Then enter `cd katapult` to navigate to the Katapult directory.

2. Enter `make menuconfig` and configure as shown in the provided image:

Katapult Firmware Options

3. Use the command `make` to compile the firmware. The resulting katapult.bin file will be in the home/username/katapult/out folder. This can be directly downloaded to your computer from the SSH software's left panel.

Katapult binary download

4. Hold the Boot button and connect the board to Raspberry Pi/CB1 via Type-C cable to enter DFU mode.

5. Enter `lsusb` in the SSH terminal to query the DFU device ID.

Querying DFU devide ID

6. Enter the following command to flash Katapult: `make flash FLASH_DEVICE=0483:df11`

> **NOTE**
> Replace `0483:df11` with the actual device ID found in the previous step.

7. After flashing, disconnect the Type-C cable.

</details>

---

<details>
<summary>Compiling Klipper Firmware for MMBv2.0</summary>

1. Connect to CB1/Raspberry Pi via SSH and enter the following commands:
`cd ~/klipper/`
`make menuconfig`

Configure the firmware as shown in the provided image (update Klipper firmware to the latest version if options are not available).

Querying DFU devide ID

`[*] Enable extra low-level configuration optionsMicro-controller`

`Micro-controller Architecture (STMicroelectronics STM32) --->`

`Processor model (STM32G0B1) --->`

If not using Katapult:

`Bootloader offset (No bootloader) --->`

If using Katapult:

`Bootloader offset (8KiB bootloader) --->`

If USB communication on Type-C is used:

`Communication interface (USB (on PA11/PA12)) --->`

If CAN-Bus communication is used:

`Communication interface (CAN bus (on PD0/PD1)) --->`
`(1000000) CAN bus speed`

2. After configuration, press `q` to exit, and select `Yes` when prompted to save.

3. Enter `make` to compile the firmware. The resulting `klipper.bin` file will be in the `home/username/klipper/out` folder. This can be directly downloaded to your computer from the SSH software's left panel.

Klipper binary download

</details>

---

<details>
<summary>Firmware Update via Katapult for MMB (CANBus only)</summary>

Guide to update Raspberry Pi / CB1 / primary MCU via CANBus using Katapult. These steps are identical for MMBv1.1 and MMBv2.0.

1. Connect the CAN bus cable and plug a jumper at the 120R terminal resistor.

2. Enter the command `cd ~/katapult/scripts` then enter `python3 flash_can.py -i can0 -q`
This will query the canbus ID (make sure the CAN cable is connected and powered on) as shown in the figure below, the UUID of the device has been found:

Querying CANBus UUID

3. Enter `python3 flash_can.py -i can0 -f ~/klipper/out/klipper.bin -u be69315a613c`

> **NOTE** 
> Replace `be69315a613c` with the actual device UUID found in the previous step.

klipper.bin needs to be generated in advance using the `make` command, and the application start offset of Katapult is 8KiB offset, so Klipper's menuconfig Bootloader offset should also be 8KiB bootloader as shown in the following figure.

CANBus Flashing Success

4. Query again with `python3 flash_can.py -i can0 -q`
The Application should now show Klipper, indicating it is running correctly.

Klipper flashing success
</details>

---

<details>
<summary>Firmware Update for MMB using USB (DFU Mode)</summary>

Guide to update Raspberry Pi / CB1 / primary MCU via USB (DFU Mode). These steps are identical for MMBv1.1 and MMBv2.0.

1. Hold the Boot button and connect the MMB to Raspberry Pi/CB1 via Type-C cable to enter DFU mode.

2. Enter `lsusb` in the SSH terminal to query the DFU device ID.

Querying DFU Mode Device ID

3. Enter `cd klipper` to navigate to the Klipper directory, and enter:

`make flash FLASH_DEVICE=0483:df11`

> **NOTE **
> Replace `0483:df11` with the actual device ID found in the previous step.

This will start flashing the firmware.

4. After flashing, enter `ls /dev/serial/by-id/` to query the device's Serial ID (only applicable for USB communication, not for CANBus).

5. If you are using USB communication, you don't need to press the Boot button for subsequent updates. You can enter the following command to flash the firmware:

`make flash FLASH_DEVICE=/dev/serial/by-id/usb-Klipper_stm32g0b1xx_4550357128922FC8-if00`

> **NOTE**
>  Replace `/dev/serial/by-id/xxx` with the actual ID found in the previous step.

6. If you are using CAN bus for communication, disconnect the Type-C cable after flashing.

</details>

---

<details>
<summary>Compiling and flashing Klipper onto EASY-BRD</summary>

This guide assumes you are using the version with Seeeduino XIAO.
Other microcontrollers configurations are available in [config](https://github.com/Tircown/ERCF-easy-brd/blob/main/config/Seeeduino%20XIAO%20-%20SAMD21G18/ercf_hardware.cfg).

* Install bossac (version ≥1.8)
```
sudo apt install libreadline-dev libwxgtk3.0-*
git clone https://github.com/shumatech/BOSSA.git
cd BOSSA
make
sudo cp bin/bossac /usr/local/bin
```
* Prepare the firmware
```
cd ~/klipper
make menuconfig
```
Menuconfig instructions
```
make clean
make
```
* Flashing the Seeeduino XIAO
Connect the Seeeduino XIAO to your raspberry if it's not already done.
Get the port of the XIAO, i.e. `ls /dev/tty*`, and modify the default `/dev/ttyACM1` in the command line bellow.
Use tweezers or short lines to short the RST pins in the diagram twice. The orange LED lights flicker on and light up. Then send in the next few seconds this command line matching your port.
```
sudo /usr/local/bin/bossac -i -d -p /dev/ttyACM1 -e -w -v -R --offset=0x2000 out/klipper.bin
```

More informations on how to reset for flashing:
https://wiki.seeedstudio.com/Seeeduino-XIAO/#enter-bootloader-mode
</details>

---

<details>
<summary>Other EASY-BRD MCU configurations</summary>

See [ercf_hardware.cfg](https://github.com/Tircown/ERCF-easy-brd/blob/main/config/Seeeduino%20XIAO%20-%20SAMD21G18/ercf_hardware.cfg) for the Seeeduino XIAO (most common solution)
Other microcontrollers configurations are available in config.
</details>

---

<details>
<summary>Compiling Klipper for ERBv1.0</summary>

### Compile options
On your klipper device (usually Raspberry Pi) run the following to create your make configuration:

```shell
cd  ~/klipper
make clean
make menuconfig
```

Select the following menuconfig settings

makemenuconfig

And create the firmware files by running the following:

```shell
make
```

</details>

---

<details>
<summary>Flashing Firmware onto ERBv1.0</summary>

#### 1.With your windows PC

Step 1: Connect 24V (Power on the board)

Step 2: Connect USB-C cable to your Klipper device (usually Raspberry Pi)

Step 3: Push and hold the BOOTSEL button

Step 4: Push the RST button and hold 0.5 seconds

Step 5: Release the RST button, after 3 seconds, Release the bootsel button

Step 6: `RPI-RP2` folder will show up on your computer, copy your built firmware `klipper.uf2` to the folder.





#### 2. With your Pi 

Thanks for mk-maddin's work:
https://github.com/FYSETC/FYSETC-ERB/issues/2#issuecomment-1618902635

##### Connecting the board and bring it into flash mode

Step 1: Connect 24V (Power on the board)

Step 2: Connect USB-C cable to your Klipper device (usually Raspberry Pi)

Step 3: Push and hold the BOOTSEL button

Step 4: Push the RST button and hold 0.5 seconds

Step 5: Release the RST button, after 3 seconds, Release the bootsel button

Verify your device is in boot mode connected by running the following command:

```shell
lsusb
```

The output should contain an entry looking like 2e8a:0003 Raspberry Pi RP2 Boot


##### Flashing the firmware
Now we do not flash the fimware by directly copying it to the storage, but we flash it using the following command:

```shell
make flash FLASH_DEVICE=2e8a:0003
```

The output looks like the following - IF you are prompted (you might or might not) for a password, enter the password of your current user account.


Now restart your fystec-erb by disconnecting 24V - waiting some seconds and reconnecting 24V again.
You should be able to see it as usual klipper device within 
```shell
ls /dev/serial/by-id
```

### Configuration

See `ercf_hardware.cfg` in the ERBv1.0 repository [config](https://github.com/FYSETC/FYSETC-ERB/tree/main/V1.0/config) folder.

### Known issues

The mark of GPIO24 and GPIO25 is swapped, check the silk file [here](https://github.com/FYSETC/FYSETC-ERB/blob/main/hardware/Silk%20Fixed.pdf).
</details>

---

<details>
<summary>Compiling and Flashing Klipper onto ERBv2.0</summary>

### Compile and upload
In order to compile and upload at one time, you need to follow the steps below to put RP2040 into dfu mode.

1. Step 1: Connect 24V (Power on the board)
2. Step 2: Connect USB-C cable to your Klipper device (usually Raspberry Pi)
3. Step 3: Push and hold the BOOTSEL button
4. Step 4: Push the RST button and hold 0.5 seconds
5. Step 5: Release the RST button, after 3 seconds, Release the bootsel button
6. Verify your device is in boot mode connected by running the following command:

```shell
lsusb
```

The output should contain an entry looking like 2e8a:0003 Raspberry Pi RP2 Boot


On your klipper device (usually Raspberry Pi) run the following to create your make configuration:

```shell
cd  ~/klipper
make clean
make menuconfig
```

Select the following menuconfig settings

Use USB communication



Use CANBUS communication



And create and upload the firmware files by running the following:

```shell
make flash FLASH_DEVICE=2e8a:0003
```
The output looks like the following - IF you are prompted (you might or might not) for a password, enter the password of your current user account.


Now restart your fystec-erb by disconnecting 24V - waiting some seconds and reconnecting 24V again.
Or press the reset button for one second and then release it.
You should be able to see it as usual klipper device within 
```shell
ls /dev/serial/by-id
```
### Configuration

See `ercf_hardware.cfg` in the ERBv2.0 repository [config](https://github.com/FYSETC/FYSETC-ERB/tree/main/V2.0/config) folder.

---------------------------------------------------

> **TIP**
> We recommend using the Katapult bootloader, whether you use USB or CANBUS communication. This can avoid many strange problems.
> 
> Configuration of the Katapult bootloader:
> 
> ERBv2_katakulpt_menuconfig_USB
> ERBv2_katakulpt_menuconfig_CAN
> 
> Configuration of klipper using Katapult:
> 
> ERBv2_menuconfig_16kb_USB
> ERBv2_menuconfig_16kb_CAN

</details>

---

### ERCF Setup Steps:
- Flashing Your Local MCU
- [Installing Happy Hare](https://github.com/Enraged-Rabbit-Community/ERCFv2.5/blob/main/Documentation/Installing-Happy-Hare.md)
- [Happy Hare Configuration](https://github.com/Enraged-Rabbit-Community/ERCFv2.5/blob/main/Documentation/Happy-Hare-Configuration.md)
- [Hardware Configuration Checks](https://github.com/Enraged-Rabbit-Community/ERCFv2.5/blob/main/Documentation/Hardware-configuration-checks.md)
- [Hardware Calibration](https://github.com/Enraged-Rabbit-Community/ERCFv2.5/blob/main/Documentation/Hardware-Calibration.md)
- [Toolhead Distances](https://github.com/Enraged-Rabbit-Community/ERCFv2.5/blob/main/Documentation/Toolhead-Distances.md)
- [Installing KlipperScreen Happy Hare](https://github.com/Enraged-Rabbit-Community/ERCFv2.5/blob/main/Documentation/Installing-KlipperScreen.md)
- [Slicer Setup](https://github.com/Enraged-Rabbit-Community/ERCFv2.5/blob/main/Documentation/Slicer-Setup.md)
- [Further Mods to Consider](https://github.com/Enraged-Rabbit-Community/ERCFv2.5/blob/main/Documentation/Further-Mods.md)

#### Even more Happy Hare info can be found at:
- [Happy Hare Wiki](https://github.com/moggieuk/Happy-Hare/wiki)

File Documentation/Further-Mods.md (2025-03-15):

## #f03c15 #c5f015 #1589F0 Further Mods to Consider

A toolhead filament cutter (eg Filametrix) or Selector filament cutter (eg EREC) will remove the need to tune your filament tips. It is widely considered to be a very worthwhile modification, because [tip tuning](https://github.com/moggieuk/Happy-Hare/wiki/Tip-Forming-and-Purging) is a lengthy manual process that must be done for each new filament type and brand, and potentially even for each color or batch of filament. Toolhead cutters are recommended over Selector filament cutters because of the chance for strings of filament to be left in the Bowden tube.

Extruder and/or toolhead filament sensors are also recommended options because they add more automation to Happy Hare's functionality. All toolhead distances can be automatically derived when using both sensors - without them, some amount of trial and error is needed to adjust the toolhead distances. This is important for both loading, unloading, and ooze prevention.

Because there are a multitude of different extruders and toolheads, there is no single cut-and-dry solution for toolhead filament cutters or sensors. The ERCF team is working on developing suitable first-part extruder and toolhead options. One of the first to be released after ERCF v2.5 is out of beta will be a modified Clockwork2 extruder with dual sensor options, a toolhead cutter, and other quality-of-life improvements. Stay tuned!

[Blobifier](https://github.com/Dendrowen/Blobifier) is a modification that allows for purging filament to pellets, instead of using a Wipe Tower. Happy Hare includes optional support for Blobifier that can be enabled either during initial setup.

### ERCF Setup Steps:
- [Flashing Your Local MCU](https://github.com/Enraged-Rabbit-Community/ERCFv2.5/blob/main/Documentation/Flashing-Local-MCU.md)
- [Installing Happy Hare](https://github.com/Enraged-Rabbit-Community/ERCFv2.5/blob/main/Documentation/Installing-Happy-Hare.md)
- [Happy Hare Configuration](https://github.com/Enraged-Rabbit-Community/ERCFv2.5/blob/main/Documentation/Happy-Hare-Configuration.md)
- [Hardware Configuration Checks](https://github.com/Enraged-Rabbit-Community/ERCFv2.5/blob/main/Documentation/Hardware-configuration-checks.md)
- [Hardware Calibration](https://github.com/Enraged-Rabbit-Community/ERCFv2.5/blob/main/Documentation/Hardware-Calibration.md)
- [Toolhead Distances](https://github.com/Enraged-Rabbit-Community/ERCFv2.5/blob/main/Documentation/Toolhead-Distances.md)
- [Installing KlipperScreen Happy Hare](https://github.com/Enraged-Rabbit-Community/ERCFv2.5/blob/main/Documentation/Installing-KlipperScreen.md)
- [Slicer Setup](https://github.com/Enraged-Rabbit-Community/ERCFv2.5/blob/main/Documentation/Slicer-Setup.md)
- Further Mods to Consider

#### Even more Happy Hare info can be found at:
- [Happy Hare Wiki](https://github.com/moggieuk/Happy-Hare/wiki)

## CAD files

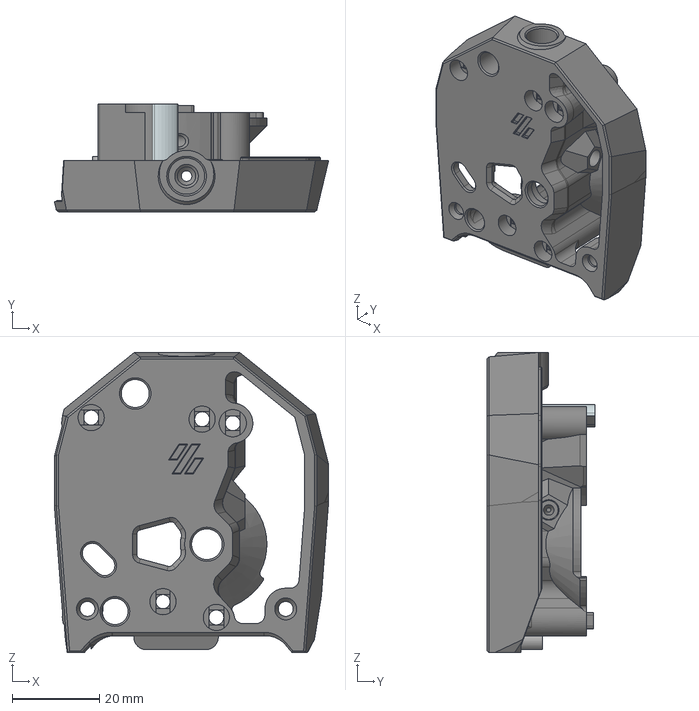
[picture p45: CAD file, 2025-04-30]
Recommended_Options/Filametrix_v2/CAD/CW2_new_motor_plate/SB_CW2_new_motor_plate_Main_Buddy_Cutting_with_ECAS.stp
62.8 x 24.7 x 68.7 mm

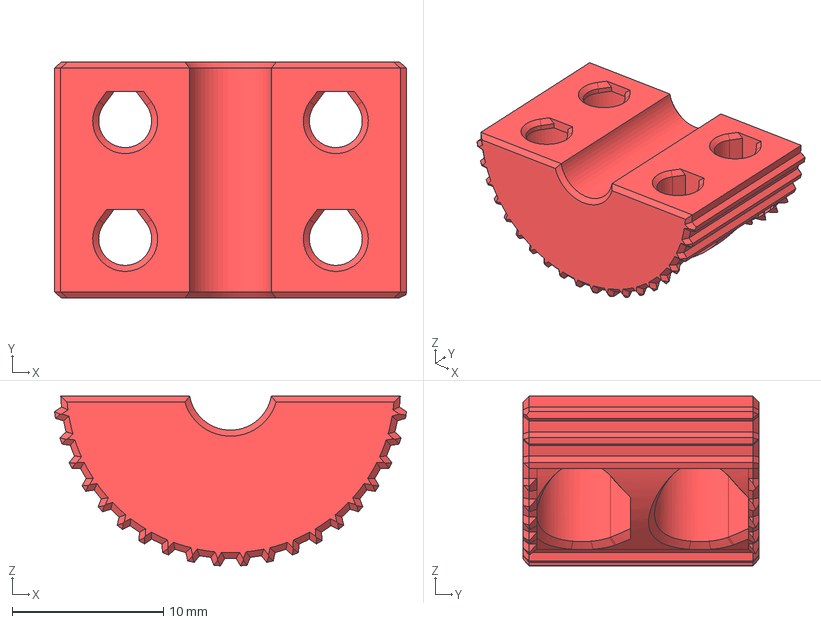
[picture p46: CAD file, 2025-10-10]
CAD/Misc/[a]_5mm_Split_Coupler_V0.step
23.3 x 15.6 x 11.2 mm

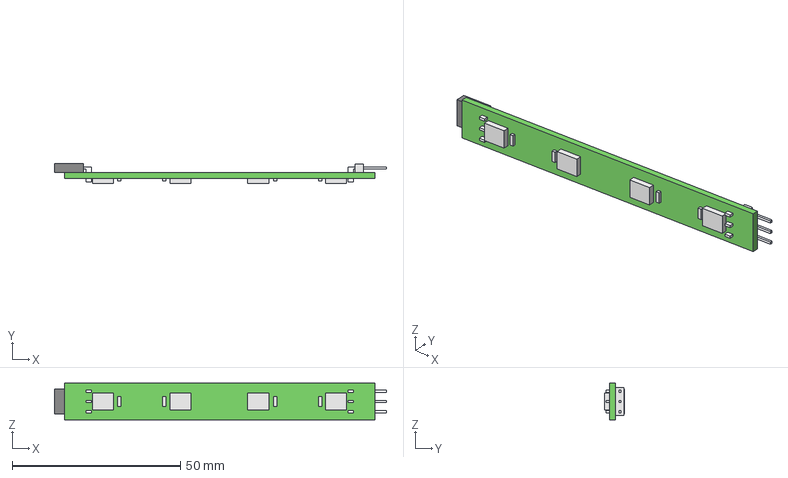
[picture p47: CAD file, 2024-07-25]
CAD/Misc/Apron_Neopixels/ERCF Carrot on a Stick v2.step
98.6 x 6.05 x 10.9 mm
LEDs
Capacitors
PCB
Connector
Header Comb
Header 1
Header 2

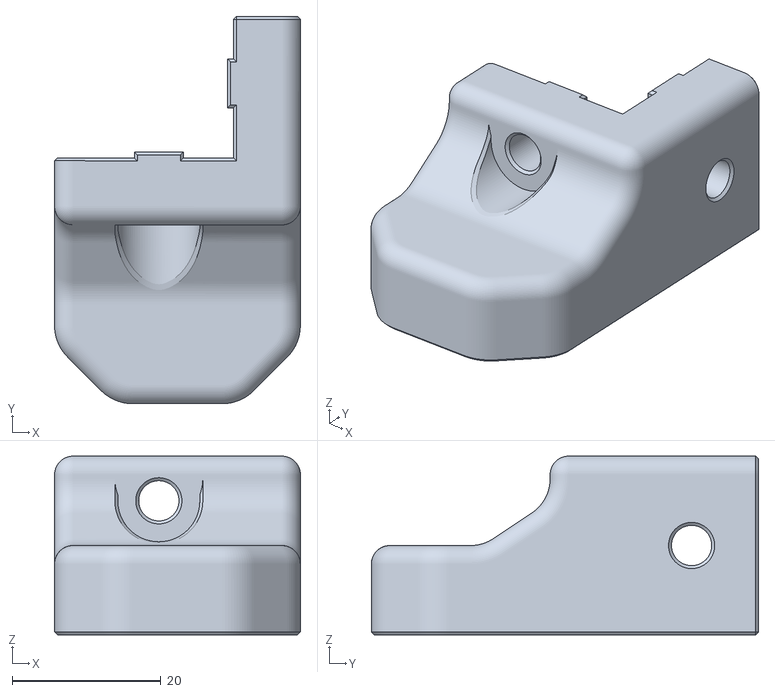
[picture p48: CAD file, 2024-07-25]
Mounting/Supports/Adjustable_Mount/2020/2020_Mount.stl
33.0 x 52.0 x 24.0

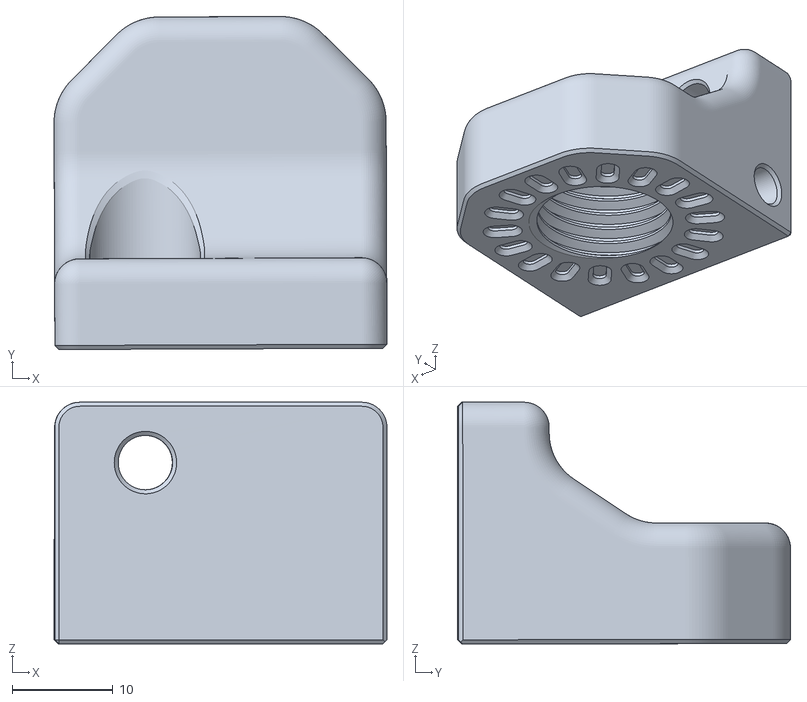
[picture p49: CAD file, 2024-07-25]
Mounting/Supports/Adjustable_Mount/3030_(SW_with_panels)/3030_Flat_Mount_Mirrored.stl
33.1 x 33.1 x 24.0

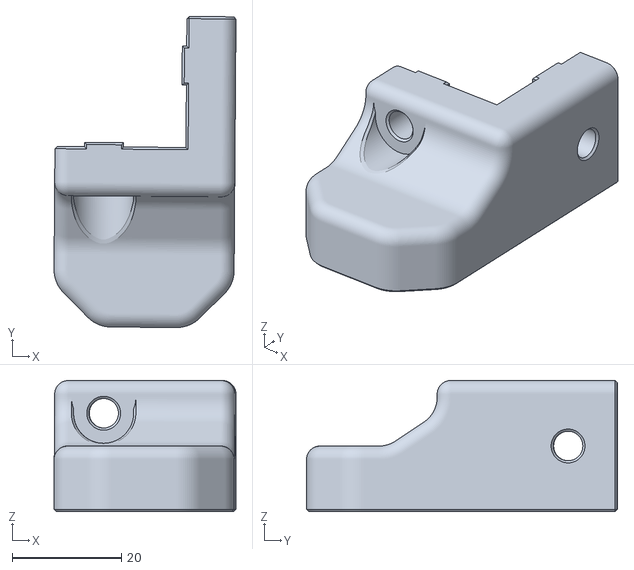
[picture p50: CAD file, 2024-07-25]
Mounting/Supports/Adjustable_Mount/3030_(SW_without_panels)/3030_Mount.stl
33.3 x 57.0 x 24.0

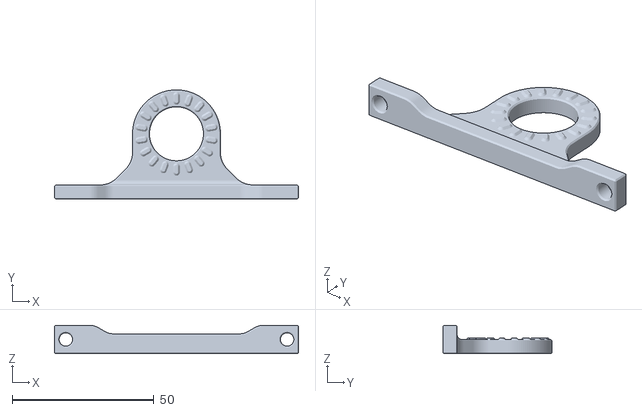
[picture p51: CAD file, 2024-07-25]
Mounting/Supports/Adjustable_Mount/Junction_Plate_Flat_x2.stl
86.0 x 38.5 x 10.0

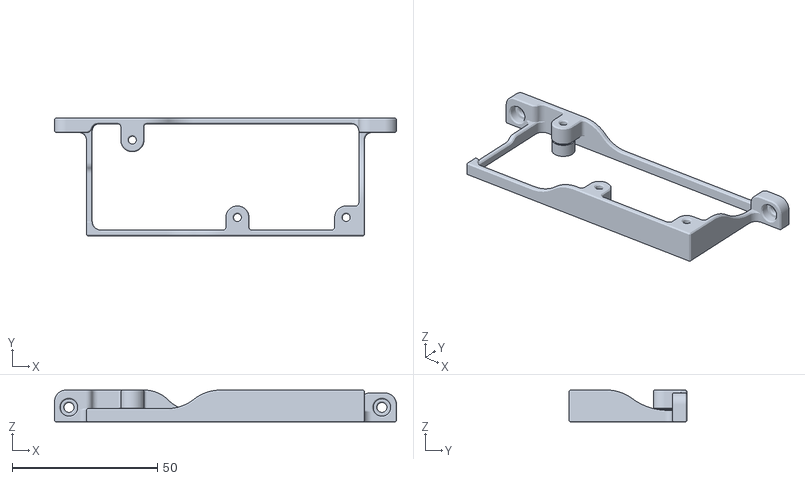
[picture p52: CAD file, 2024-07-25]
Mounting/Supports/Adjustable_Mount/Option/ERCF_Easy_Brd_Bracket_Mount.stl
117.8 x 40.6 x 11.0

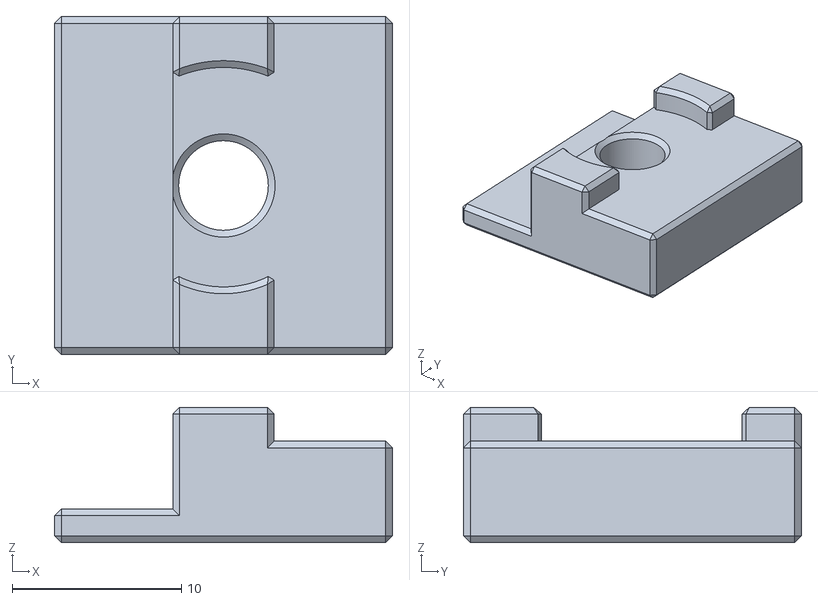
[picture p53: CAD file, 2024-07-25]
Mounting/Supports/V1_V2/[a]_Support_Feet_4mm_x4.stl
20.0 x 20.0 x 8.00

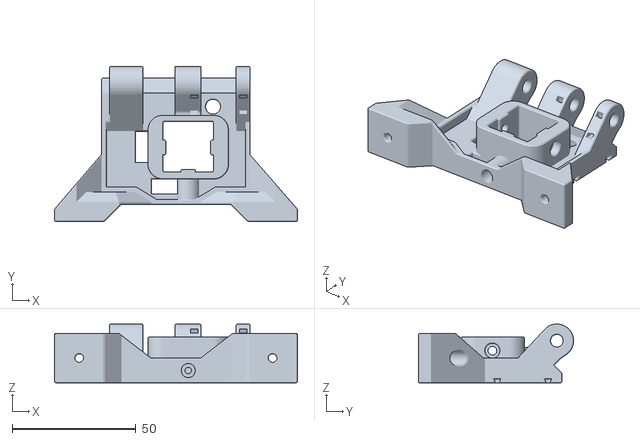
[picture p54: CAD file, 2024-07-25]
Recommended_Options/ERCT_Buffer_V3/Endblock/End_Block_LRF.stl
98.0 x 62.6 x 23.7

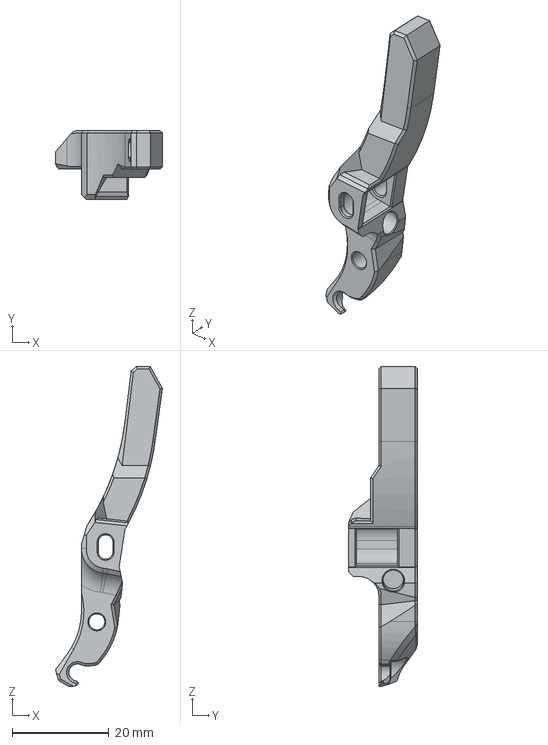
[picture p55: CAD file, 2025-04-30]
Recommended_Options/Filametrix_v2/CAD/Cutting_Arm.stp
22.1 x 14.2 x 66.1 mm

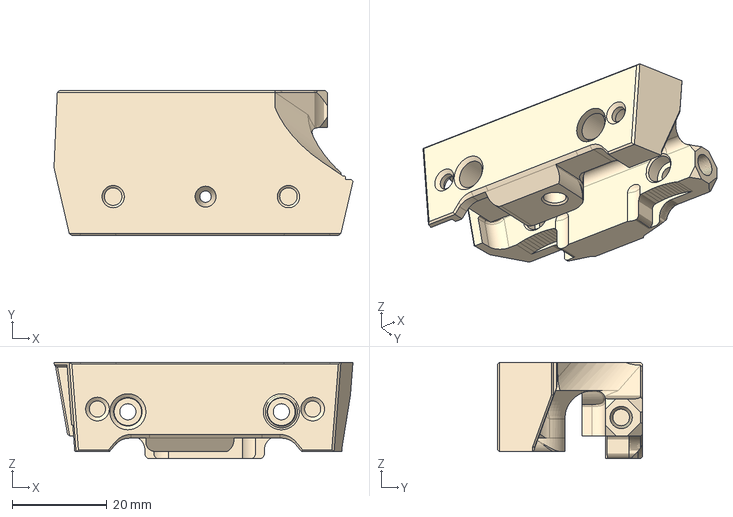
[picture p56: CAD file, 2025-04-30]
Recommended_Options/Filametrix_v2/CAD/StealthOrbiter/ORBITERMOUNT_No_Sensor_V3_Cutting v2.stl.step
63.1 x 30.6 x 20.4 mm

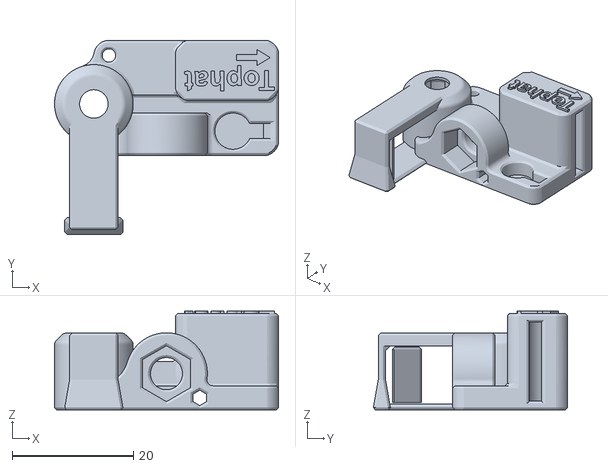
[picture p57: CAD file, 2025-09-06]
STLs/0._Tools/Calib_test_For_C9_v24.stl
37.0 x 32.1 x 16.4

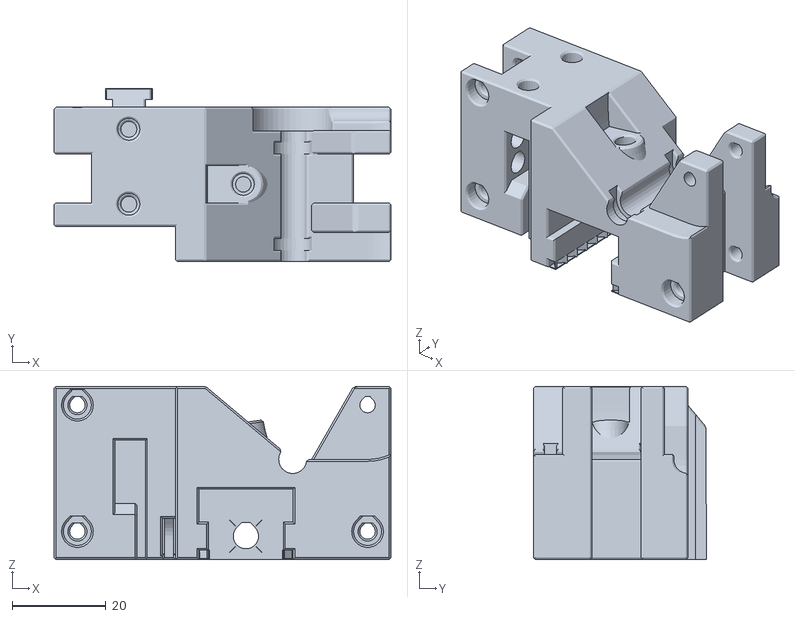
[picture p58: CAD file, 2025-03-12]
STLs/1._Gear_Box_Part_1/Gearbox_v61.stl
72.0 x 37.0 x 37.0

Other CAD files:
Recommended_Options/Filametrix_v2/CAD/CW2_new_motor_plate/SB_CW2_new_motor_plate_Main_Buddy_Cutting_with_M6.stp
STLs/2._Motor_Mounts_Drive_Shaft/2.3_Drive_Shaft/[a]_Customizable_Split_Coupler_B.3mf
STLs/2._Motor_Mounts_Drive_Shaft/Alternate_Motor_Mounts/Motor_Mount_NEMA17_Pancake_Direct_Drive_v31.stl
STLs/2._Motor_Mounts_Drive_Shaft/Logo_Mask_v33.stl
CAD/Misc/1.8_LRF_Gear_Box_Bottom_Panel_V3.0.step
CAD/Misc/Apron_Neopixels/ERCF Carrot on a Stick v2.f3d
CAD/Misc/Apron_Neopixels/LED_Soldering_Tool_24mm.f3d
CAD/Misc/Apron_Neopixels/Neopixel_Apron_Led_Holder.step
CAD/Misc/Apron_Neopixels/Neopixel_apron_PCB_Led_Holder.step
CAD/Misc/Calib_Test_For_C9 v2.step
CAD/Misc/Calib_Test_redux.step
CAD/Misc/ERCF Carrot on a Stick v2.f3d
CAD/Misc/ERCF LED PCB Mount v9.f3d
CAD/Misc/Encoder_v23.step
CAD/Misc/End_Block_LRF_V3.step
CAD/Misc/Filament Block C10D v26.step
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

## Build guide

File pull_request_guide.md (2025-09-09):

# Pull Request Guide

The following is a basic guide for creating pull requests for submitting to any of the ERCF repositories such as Mounting and User_Mods.

1. Create a github user if you don't have one already.
2. Browse to the ERCF github repo, either User_Mods or Mounting.
3. On the top right, click on 'Fork'.
4. It will process for a few seconds, then return back with a fork of the selected repository.  The owner will no longer be 'ERCF', but the user who forked the repository.
5. Make the desired changes to the local / forked repository.  This can be done from the web UI or the command line.
6. Be sure to create a commit.  This actually adds the files to the request.
7. Return back to the main ERCF repo by clicking the link next to "forked from ERCF/"
8. Select Pull Requests and click the New Pull Request button.
9. Select Compare Across Forks and select your repository.
10. Give a title for your pull request and fill out the form.
11. Click Create Pull Request. It will be submitted and will be manually reviewed.

For a visual reference, please see [Nemgrea's video guide](https://i.imgur.com/qQo0DxR.gifv)

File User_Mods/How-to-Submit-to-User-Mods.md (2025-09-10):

Because mounting is specific to your printer, mounting is left for the community to do. 

# Community Submission Information

The following are guidelines for submitting documentation to the ERCF Mounting repo. This is to provide a consistent format for the resulting documentation and information.

## How to Submit your Design

Each submitter should create a directory for their user. The directory name should preferably be the same as their Discord username or Github username. Each guide should be named accordingly but include the markdown ".md" extension (e.g. 'how\_to\_build\_ercf.md'). If there are images to be included, it is recommended to create an 'images' subdirectory for all of the images and link to those in the guide.

Each pull request should also update the associated index.md with a link to the macro and the creator's username.

# Pull Requests

How to create [Github pull requests](./../pull_request_guide.md)

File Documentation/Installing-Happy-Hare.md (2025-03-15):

*\[This page has been taken from the Happy Hare Wiki (Thanks Moggie!) and modified to be specific to ERCF v2.5.\]*

#### Page Sections:
- [Cloning Happy Hare Repo](#---cloning-happy-hare-repo)
- [Running Installer](#---running-installer)
- [Creating Base Klipper Config](#---creating-base-klipper-config)
- [Pause/Resume/Cancel_Print Macros](#---pauseresumecancel_print-macros)
- [Upgrading](#---upgrading)

*\[This guide is copied directly from the [Happy Hare Installation](https://github.com/moggieuk/Happy-Hare/wiki/Installation) page. Thanks Moggie!\]*

This section deals with installing Happy Hare to the host computer (most commonly the Raspberry Pi). Basically, the installation proceeds as with any other git based software, indeed like Klipper itsself.

Happy Hare consists of a set of Klipper "extra" modules, a moonraker "component" and a set of macros and configuration files. To install you must first clone from Github and then install using the supplied install script. This install will both setup a base set of klipper configuration files as well as creating the symlinks necessary to link the cloned files into your Klipper/Moonraker installation.

Once installed it will be added to Moonraker update-manager for easy updates like other Klipper plugins.

<br>
 
## #f03c15 #c5f015 #1589F0 Cloning Happy Hare Repo

The first step is to clone the Happy Hare repository onto your Raspberry Pi. If you're unfamiliar with cloning, it just copies all the data in the git repository to your local computer. Since the Happy Hare git has all the necessay software, we use the `git clone` functionality to pull everything from github to the local computer (the rpi, in most cases of Klipper). So, go ahead and log into your rpi via ssh.

In power shell, and with Mainsail, this will look like this:  

```yml
ssh pi@mainsailos.local
```  

> [!NOTE]  
> You will notice in the following pictures the bash prompt is `Miriax@VoronRed:~`. Yours won't look like that. It will be `username@<hostname.:~` where the hostname is likely "mainsailos" or the ip address.

Alternatively, you can use your Klipper ip address, which will look something like this:  
```
ssh username@192.168.0.256
```  
(You'll need to change the username and ip address.)  

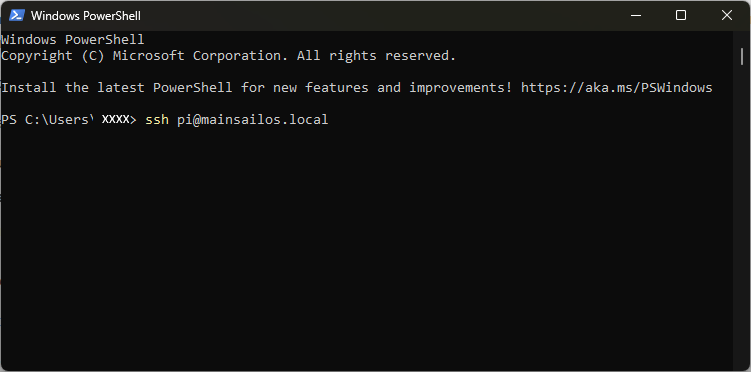
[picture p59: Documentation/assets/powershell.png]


From there, you're going to clone Happy Hare software to your rpi:  

```yml
cd ~
git clone https://github.com/moggieuk/Happy-Hare.git
```

(it's ok to click the copy icon and right click in the ssh terminal to paste or just type it out if you want.)  
Let that finish. It should only take a few seconds, and you'll now have your very own copy of Happy Hare stored on your rpi!
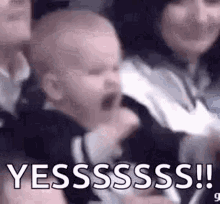
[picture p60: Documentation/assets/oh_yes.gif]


Now, you're going to change to the Happy Hare directory using the `cd` command (`cd` is Linux Geek for "change directory"):  

```yml
cd Happy-Hare
```

Here is a picture of the previous steps successfully performed:
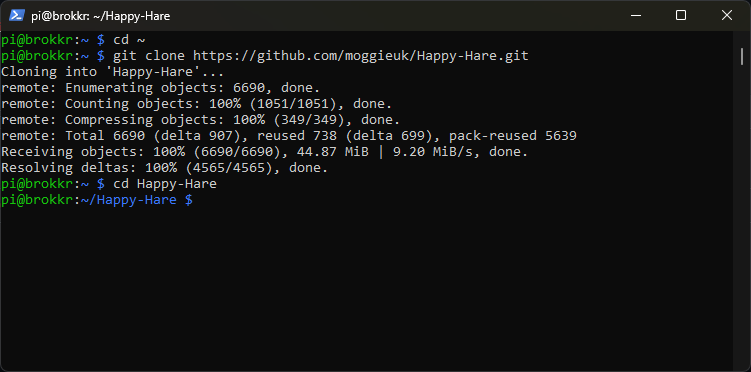
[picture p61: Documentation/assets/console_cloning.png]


<br>
 
## #f03c15 #c5f015 #1589F0 Running Installer

The install does not ship a set of template config files, instead you can create your starting templates by running the installer in interactive mode. This will ask questions that will be used to generate and install the template config. See [next section](#---creating-base-klipper-config). Read this section to familiarize yourself with command line options and determine if you need to use `-c`, `-k` or `-r` flags.

You'll be asked to run:

```
cd ~/Happy-Hare
./install.sh -i
```

The `-i` option will bring up an interactive installer to aid setting some confusing parameters. For popular external mcu boards it will also configure all the pins for you. If run without with the `-i` flag it defaults to updating the current installation which is sometimes necessary for significant version updates (see [here](Upgrade-Notice)). Note that if an existing install is found it will never be overwritten, it will be moved to a numbered backup folder with a `<file>.<date>` extension and current configuration defaults carried over. If you still choose not to install the new `mmu*.cfg` files automatically you can copy the templates and fill in all the tokens and blank parameters by hand. Frankly it is much easier to run through an initial install and use the generated config files as a starting point.
<br>

Note that the installer will look for Klipper install and config in standard locations. If you have customized locations or multiple Klipper instances on the same rpi, or the installer fails to find Klipper you can use the `-k` and `-c` flags to override the Klipper home directory and Klipper config directory respectively. Also, if installing on Repetier-Server add the `-r` option. E.g.
```
./install.sh -k /opt/klipper/LK5_Pro_ERCF -c /var/lib/Repetier-Server/database/klipper -m /opt/klipper/LK5_Pro_ERCF/moonraker -r LK5_Pro_ERCF -i
```

If you have multiple Klipper instances installed with for example Kiauh. You can use the `-a` flag to specify the service name. E.g.
```
./install-sh -a klipper-two -k <klipper_home_dir> -c <klipper_config_dir>
```

<br>

> [!IMPORTANT]  
> `mmu.cfg`, `mmu_hardware.cfg`, `mmu_macro_vars.cfg` & `mmu_parameters.cfg` (and other base config files) must all be referenced by your `printer.cfg` master config file with `mmu.cfg` and `mmu_hardware.cfg` listed first (the recommended way to achieve this is simply with `[include mmu/base/*.cfg]`). `mmu/optional/client_macros.cfg` should also explicitly be referenced if you don't already have working PAUSE / RESUME / CANCEL\_PRINT macros (but be sure to read the section beforehand regarding macro expectations and review the default macros). The install script can also include these optional config files for you.
<br>

> [!TIP]  
> If you are concerned about running `install.sh -i` then run like this: `install.sh -i -c /tmp -k /tmp` This will build the `*.cfg` files for you but put then in /tmp rather than overwriting your active configuration. You can then refer to them, pulling out the bits you need to augment your existing install or simply see what answers to the various questions will do...

```
Usage: ./install.sh [-a <kiauh_alternate_klipper>] [-k <klipper_home_dir>] [-c <klipper_config_dir>] [-m <moonraker_home_dir>] [-b <branch>] [-r <repetier_server stub>] [-i] [-d] [-z]

-i for interactive install
-d for uninstall
-b to switch to specified feature branch (sticky)
-z skip github check (nullifies -b <branch>)
-r specify Repetier-Server <stub> to override printer.cfg and klipper.service names
-a <name> to specify alternative klipper-service-name when installed with Kiauh.
-c <dir> to specify location of non-default klipper config directory
-k <dir> to specify location of non-default klipper home directory
(no flags for safe re-install / upgrade)
```

<br>
 
## #f03c15 #c5f015 #1589F0 Creating Base Klipper Config

### Running the installation script
Finally, you'll install Happy Hare using a bash script which contains all the commands necessary to install Happy Hare:  

```
./install.sh -i
```  

> [!NOTE]  
> Here, we're using the `-i` switch (switch is more Linux Geek for "option") to activate an interactive install. This will help guide you through setting most basic options for your MMU. This is generally only needed for the first install. Upgrading can be done by `./install.sh` with no switches.

You'll be asked a series of questions pertaining to your hardware and options.

### 1.  MMU Type
Choose ERCFv2.0 from the list.

> [!NOTE] 
> There will be an ERCFv2.5 option soon, but for now we must pick v2.0

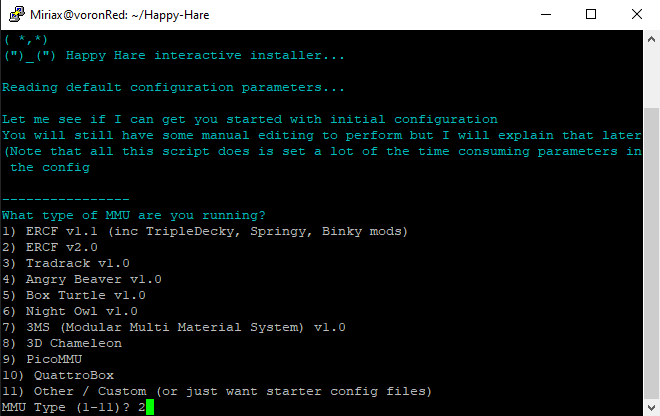
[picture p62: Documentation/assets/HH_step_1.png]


### 2. Number of Gates
Happy Hare installer then asks for the number of gates.  

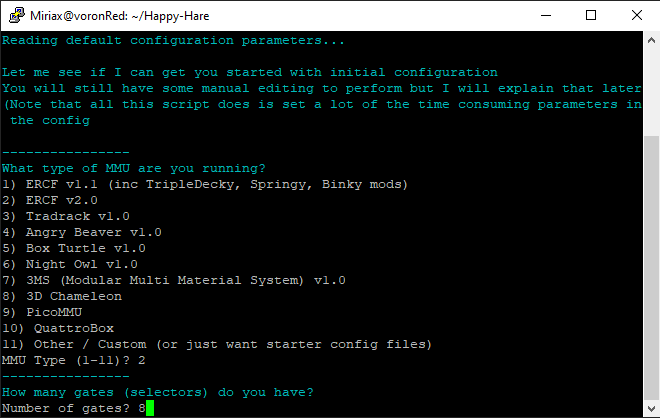
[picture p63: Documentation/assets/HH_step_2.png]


Enter the correct number of gates for your ERCF, usually 8 in v2.5.

#### 3. Control Board
Select the type of control board you have installed. MMBv1.1 and MMBv2.0 are the recommended boards for ERCFv2.5.

*\[This graphic will be updated soon\]*

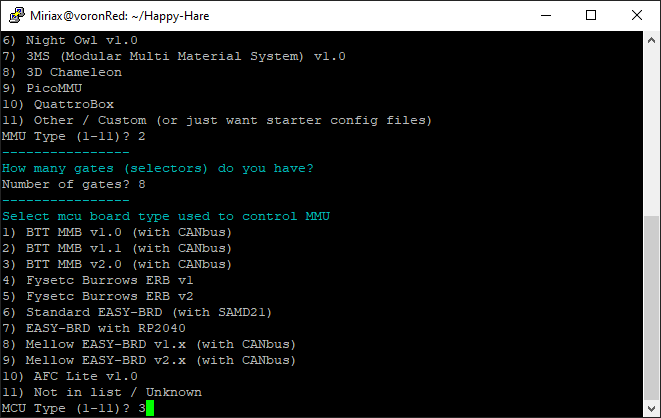
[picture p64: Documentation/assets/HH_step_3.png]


#### 4. Control Board Address
Happy Hare will then attempt to figure out where your control board is. So far, this doesn't work for CANBUS boards. If your printer's mainboard is connected, that will be detected instead, so input "N," unless you're using a Remote MCU setup.

> [!NOTE]
> If you followed the previous guide on [Flashing Your Local MCU](https://github.com/Enraged-Rabbit-Community/ERCFv2.5/blob/main/Documentation/Flashing-Local-MCU.md), you should already know your CANBus UUID. You will need to manually add the CANBus UUID to the top of your mmu.cfg. If you are using USB instead, this should work and find your board!

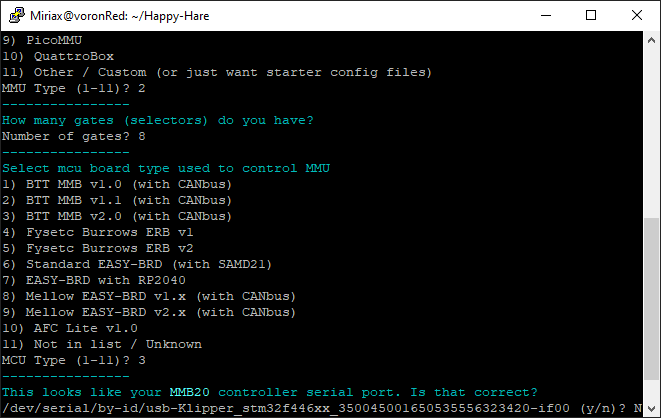
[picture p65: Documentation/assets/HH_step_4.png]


#### 5. LED Options
If you have neopixels installed on your ERCF, enable them here.  

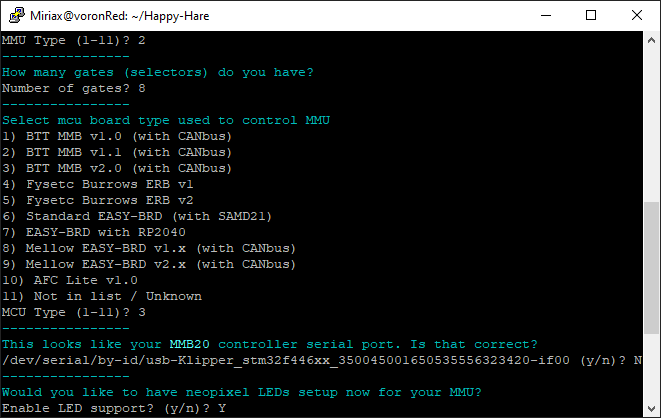
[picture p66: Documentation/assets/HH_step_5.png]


#### 6. Selector Touch Operation
Decide whether or not to enable Selector Touch operation. This can help with recovery of an error, but is also a bit difficult to get set up properly. It's better to say "no" and get it working after you're more familiar with the ERCF and Happy Hare.

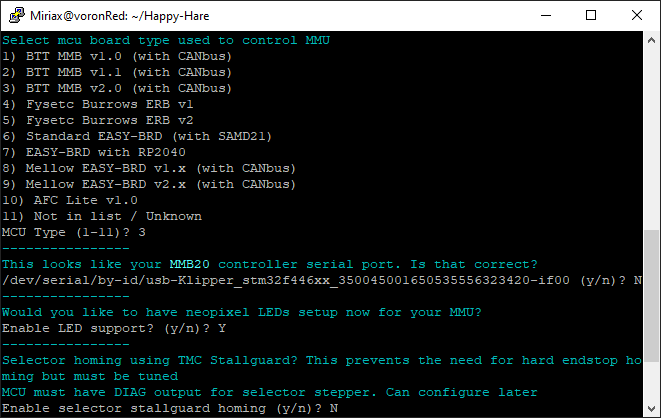
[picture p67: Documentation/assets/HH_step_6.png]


#### 7. Servo Options
Select your servo option from the list.

> [!NOTE] 
> You're going to adjust the angles later, so this doesn't matter too much right now. During Beta Testing, this is something we'll ask you to report on so that we can make more accurate presets.

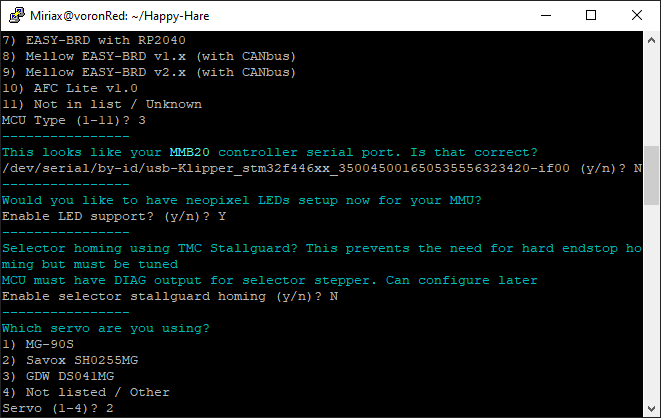
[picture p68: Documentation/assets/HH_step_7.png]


#### 8. Clog detection
With Binky, It's probably best to enable clog detection and set it to automatic. This acts like a smart filament sensor and will pause the print if something goes bad with the filament feed.  

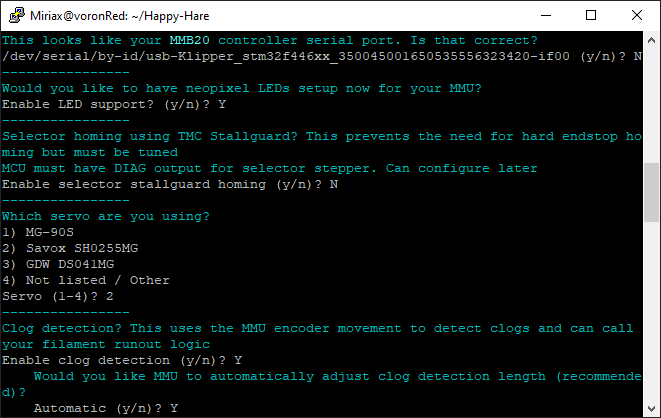
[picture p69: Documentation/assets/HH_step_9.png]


#### 9. EndlessSpool
Happy Hare has the capability to map multiple gates to one tool. This allows for "endless spool" operation. When one spool runs out, if you have the same material and color mapped to another gate, it will automatically switch to the other gate and resume printing. This option is recommended for long prints.

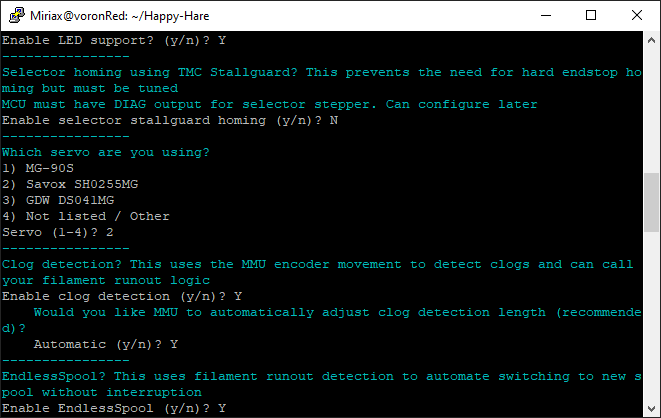
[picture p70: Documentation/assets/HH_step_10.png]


#### 10. Final step
The last step asks to add the `[include mmu*]` lines to your printer.cfg. **On initial setup it is recommended to select yes.** If Happy Hare has already been installed, you should select "no."

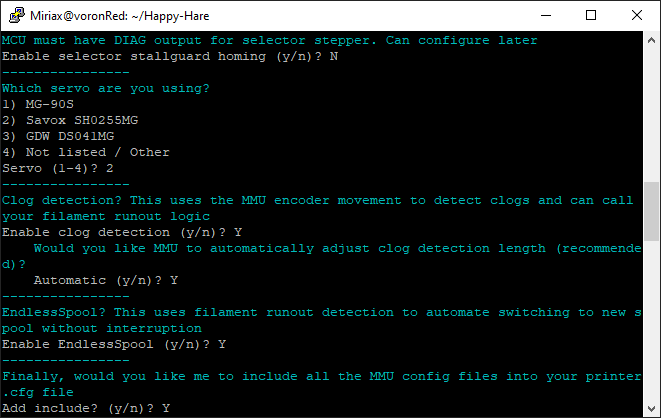
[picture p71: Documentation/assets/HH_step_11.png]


From here, Happy Hare will install itself with the options you've selected. You should have a nice little report that Happy Hare is ready:  

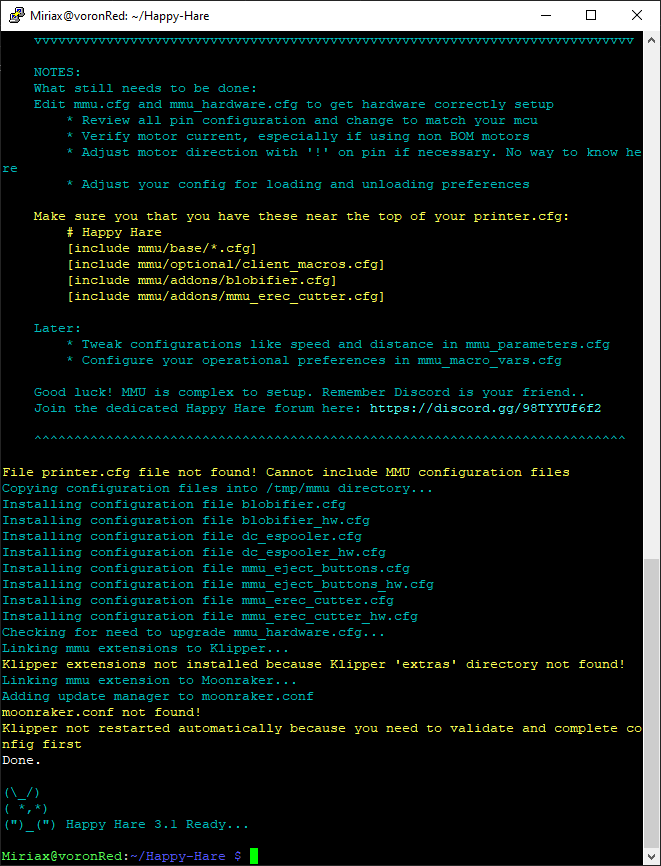
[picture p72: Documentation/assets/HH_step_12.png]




> [!NOTE] 
> During Beta testing, and really any time it happens, **please report any misfires by the automatic setup!**

Once this has been run sucessfully you will have outline configuration files installed. Happy Hare creates a hierachy of files in the klipper config directory. To review the layout and purpose of each of these files read [Configuration Reference](https://github.com/moggieuk/Happy-Hare/wiki/Configuration-Reference)

Now, you have Happy Hare installed on your rpi. Feels good, doesn't it?  
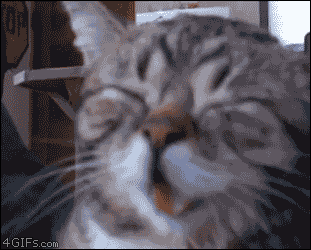
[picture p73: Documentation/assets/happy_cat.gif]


<br>

## #f03c15 #c5f015 #1589F0 Pause/Resume/Cancel\_Print Macros

It is recommended that you use the PAUSE/RESUME/CANCEL\_PRINT macros aka "client macros" that are supplied with Happy Hare at least when setting up. The reason is that they are reasonably full featured and integrate with the "sequence" macros you will learn about later that control toolhead movement during a toolchange. These macros can be used by ensuring that this appears in your `printer.cfg` config after the `[include mmu/base/*.cfg]`:

> [include mmu/optional/client\_macros.cfg]

Regardless of whether you use your own or use the ones provided in `client_macros.cfg`, Happy Hare will automatically wrap anything defined so that it can inject the essential steps to control the MMU.

During a print, if Happy Hare detects a problem, it will record the print position, safely lift the nozzle up to `z_hop_height_error` at `z_hop_speed` (to prevent a blob). It will then call the user's PAUSE macro (which can be the example one supplied in `mmu_software.cfg`). As can be seen with the provided examples it is expected that pause will save it's starting position (GCODE\_SAVE\_STATE) and move the toolhead to a park area, often above a purge bucket, at fast speed.

The user then addresses the issue and calls `RESUME` to continue with the print. More on that subject can be found in Happy Hare's [Handling Errors](https://github.com/moggieuk/Happy-Hare/wiki/Handling-Errors).

The user's RESUME macro may do some purging or nozzle cleaning but is expected to return the toolhead to where it was left when the pause macro was called. At this point the Happy Hare wrapper takes over and is responsible for dropping the toolhead back down to the print and resumes printing.

Happy Hare will always return the toolhead to the correct position, but if you leave it in your park area will will move it back very slowly. You can to follow the above sequence to make this operation fast to prevent oozing from leaking on your print.

<br>

## #f03c15 #c5f015 #1589F0 Upgrading

Happy Hare is always being improved. You can update in the same way as you update Klipper through the update-manager facility in Moonraker when update is indicated. If you know an update is pending and it is not yet shown in update-manager (it can take 24h) you can force a refresh by clicking on the circular arrow.

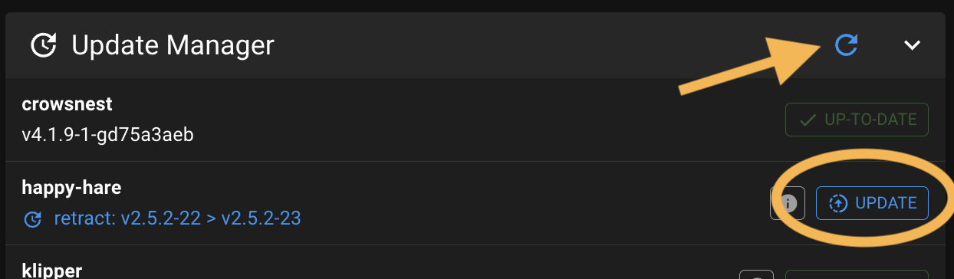
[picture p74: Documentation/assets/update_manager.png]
<p align="center"><p>

Sometimes an update includes a major change and simply upgrading through update manager is not sufficent. When this occurs you should see an error message directing you to the [Upgrade Notice](https://github.com/moggieuk/Happy-Hare/wiki/Upgrade-Notice) page (read that now because it explains major/minor/point release conventions). You will then need to run the `install.sh` script as below.

Alternatively you can simply run the following. Note that you **must not add the `-i` option to update**. This will pull the very latest code from Github and upgrade any necessary configuration files. This is also a good option to run if you suspect you have broken something or you have upgraded Klipper and it has removed the Happy Hare added modules (Hint: If you see a "step pin not defined for..." it is highly lightly that klipper has lost the Happy Hare modules and it struggling to parse the config).

```yml
cd ~/Happy-Hare
./install.sh
```

> [!TIP]  
> Don't be shy about running this. If there is nothing to update the script will do nothing and it will always backup your entire config in a directory [see config file structure](https://github.com/moggieuk/Happy-Hare/wiki/Configuration-Reference#---location-of-configuration-files) in a parallel directory with name with date stamp, similar to `mmu-20240422_102329`. The new `mmu` directory will be rebuilt extracting all the previous configuration but with updated templates. Note that an additional backup directory is created each time you run the installer uniquely date stamped.

> [!IMPORTANT]  
> If you have Klipper installed in a non-default location (i.e. you used the `-c`,`-k` or `-r` flags) you will need to add these flags again to the above, otherwise the upgrade will look in the default location and likely not find/upgrade what you expect.

### ERCF Setup Steps:
- [Flashing Your Local MCU](https://github.com/Enraged-Rabbit-Community/ERCFv2.5/blob/main/Documentation/Flashing-Local-MCU.md)
- Installing Happy Hare
- [Happy Hare Configuration](https://github.com/Enraged-Rabbit-Community/ERCFv2.5/blob/main/Documentation/Happy-Hare-Configuration.md)
- [Hardware Configuration Checks](https://github.com/Enraged-Rabbit-Community/ERCFv2.5/blob/main/Documentation/Hardware-configuration-checks.md)
- [Hardware Calibration](https://github.com/Enraged-Rabbit-Community/ERCFv2.5/blob/main/Documentation/Hardware-Calibration.md)
- [Toolhead Distances](https://github.com/Enraged-Rabbit-Community/ERCFv2.5/blob/main/Documentation/Toolhead-Distances.md)
- [Installing KlipperScreen Happy Hare](https://github.com/Enraged-Rabbit-Community/ERCFv2.5/blob/main/Documentation/Installing-KlipperScreen.md)
- [Slicer Setup](https://github.com/Enraged-Rabbit-Community/ERCFv2.5/blob/main/Documentation/Slicer-Setup.md)
- [Further Mods to Consider](https://github.com/Enraged-Rabbit-Community/ERCFv2.5/blob/main/Documentation/Further-Mods.md)

#### Even more Happy Hare info can be found at:
- [Happy Hare Wiki](https://github.com/moggieuk/Happy-Hare/wiki)

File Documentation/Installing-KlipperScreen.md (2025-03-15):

#### Page Sections:
  - [Installation](#---installation)
  - [Caveats & Possible problems / workarounds](#---caveats--possible-problems--workarounds)
  - [Font Problems](#---font-problems)
  - [Blank Screen After Update](#---blank-screen-after-system-update)
  - [Happy Hare Version Incompatibility](#---happy-hare-version-incompatibility)
  
*\[This guide is copied from the [KlipperScreen Happy Hare repo](https://github.com/moggieuk/KlipperScreen-Happy-Hare-Edition) and reformatted for ERCF. Thanks Moggie!\]*

## #f03c15 #c5f015 #1589F0 Installation
**Firstly, make sure Happy Hare software is completely up-to-date. Features were added to support this KlipperScreen add on.**

Install and setup a base KlipperScreen from the original source. Get it working. Don't skip this step because we cannot help with basic KlipperScreen and system setup.  Once you have that installed and working, log into you Rasberry Pi and execute the following commands. You can cut'n'paste...

    cd ~
    mv KlipperScreen KlipperScreen.orig
    git clone https://github.com/moggieuk/KlipperScreen-Happy-Hare-Edition.git KlipperScreen
   
    cd ~/KlipperScreen/happy_hare
    ./install_ks.sh -g <num_gates>
   
(where <num_gates> is the number of selectors you built with, e.g. 8 for a typical ERCF v2.5)
   
KlipperScreen will be restarted and hopefully you should now be running the enhanced version!

> [!NOTE]  
> Expert Tip: The last step of running './install_ks -g <num_gates>' can be run many times.. and sometimes is needed after an update to install new images or update menu structure. If you customize the MMU part of the KlipperScreen menu and want to make use of the "replicator" function that will automatically replicate menu options for the configured number of gates, you can edit menus.conf and reference the templating there.

Note that the base KlipperScreen is up-to-date (and Moggieuk will continue to merge with master every 2 weeks) with changes in the original but also includes extra menu functionality that can be used in the creation of your custom menus.  See the generated ercf_klipperscreen.conf for clues!

## #f03c15 #c5f015 #1589F0 Caveats & Possible problems / workarounds
I have only tested on a single screen.  A 640x480 resolution BTT TFT5.0.   It is possible that you might find layout problems on other (likely smaller) displays.  Also, I have only tested in and optimized for horizonal orientation.  I doubt it will be effective in vertical but I don't know of any Voron owners with vertically mounted panels.

JFYI the installer will alter or add the KlipperScreen entry in `moonraker.conf`:

    [update_manager KlipperScreen]
    type: git_repo
    path: ~/KlipperScreen
    origin: https://github.com/moggieuk/KlipperScreen-Happy-Hare-Edition.git
    env: ~/.KlipperScreen-env/bin/python
    requirements: scripts/KlipperScreen-requirements.txt
    install_script: scripts/KlipperScreen-install.sh
    managed_services: KlipperScreen

## #f03c15 #c5f015 #1589F0 Font problems:
The CSS style only specifies a "Free Mono" font to be used (the same as original KlipperScreen) for all textual displays.  I use the Unicode Box character set in that font to render the selector status, filament positions and TTG map. A couple of users have reported issues with this part of the display, either not appearing or not spaced correctly.  E.g.

mmu_panel_printing

If this occurs the first thing to try is to run the following, then restart KlipperScreen:

    sudo apt install fontconfig
    fc-cache -f -v
    sudo systemctl restart KlipperScreen

If this doesn't fix the problem I suggest installing a new font set.

> [!NOTE]  
> A very useful way of listing the fonts you have installed on your system by family is with:
> > fc-list : family | sort | uniq

<details>
<summary>🔹 How to install JetBrains fonts...</summary>

Download the JetBrains fonts from (www.jetbrains.com).  Extract the zip.  Copy all the `*.ttf` fonts (you will find them under fonts/ttf in the extracted zip) into `/usr/share/fonts/truetype` directory (you will have to sudo cp else you will likely get permission denied), then cache these fonts:

    cd <path where you extracted the font files>/fonts/ttf
    sudo cp *.ttf /usr/share/fonts/truetype
    fc-cache -f -v
     
Then finally update the font reference in the KlipperScreen css file:

    cd ~/KlipperScreen/styles

Edit the `base.css` file.  Find the css entry for `.mmu_status`, then change the font-family to:

    font-family:      JetBrains Mono;

(by default it is `font-family:     Free Mono;`)

Then restart KlipperScreen

    sudo systemctl restart KlipperScreen

If you have to do this, please let Moggieuk know the details about the operating system you are running on and how you installed KlipperScreen in the first place... if I can locate the source of the issue I might be able to workaround in the future.

</details>

## #f03c15 #c5f015 #1589F0 Blank Screen after system update
It has come to my attention that sometimes a system (OS) update can break KlipperScreen.  This is nothing to do with KlipperScreen but rather the installation of a slightly broken video driver `fbturbo`.  Luckily the fix is simple.  After OS upgrade run:

    sudo apt purge xserver-xorg-video-fbturbo

## #f03c15 #c5f015 #1589F0 Happy Hare version incompatibility
If you are upgrading and see a message like this when accessing the main MMU panel it is probably because of a version mismatch with Happy Hare on your printer.  Follow the instructions in the popup!



*All screen shots are taken with the "Colorize" theme (my preference because the buttons are more defined).  The default is z-bolt and looks slightly different.*

### ERCF Setup Steps:
- [Flashing Your Local MCU](https://github.com/Enraged-Rabbit-Community/ERCFv2.5/blob/main/Documentation/Flashing-Local-MCU.md)
- [Installing Happy Hare](https://github.com/Enraged-Rabbit-Community/ERCFv2.5/blob/main/Documentation/Installing-Happy-Hare.md)
- [Happy Hare Configuration](https://github.com/Enraged-Rabbit-Community/ERCFv2.5/blob/main/Documentation/Happy-Hare-Configuration.md)
- [Hardware Configuration Checks](https://github.com/Enraged-Rabbit-Community/ERCFv2.5/blob/main/Documentation/Hardware-configuration-checks.md)
- [Hardware Calibration](https://github.com/Enraged-Rabbit-Community/ERCFv2.5/blob/main/Documentation/Hardware-Calibration.md)
- [Toolhead Distances](https://github.com/Enraged-Rabbit-Community/ERCFv2.5/blob/main/Documentation/Toolhead-Distances.md)
- Installing KlipperScreen Happy Hare
- [Slicer Setup](https://github.com/Enraged-Rabbit-Community/ERCFv2.5/blob/main/Documentation/Slicer-Setup.md)
- [Further Mods to Consider](https://github.com/Enraged-Rabbit-Community/ERCFv2.5/blob/main/Documentation/Further-Mods.md)

#### Even more Happy Hare info can be found at:
- [Happy Hare Wiki](https://github.com/moggieuk/Happy-Hare/wiki)

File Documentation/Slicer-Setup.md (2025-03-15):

#### Page Sections:
- [Start G-Code](#---start-g-code)
- [End G-Code](#---end-g-code)
- [Toolchange G-Code](#---tool-change-g-code)
- [Customizing MMU Start/End Macros](#---customing-mmu-startend-macros)
- [MMU Error Dialog](#---mmu-error-dialog)
- [Slicer Tip Forming](#---slicer-tip-forming)
  - [Turning off slicer tip forming](#turning-off-slicer-tip-forming)
  - [Turning off slicer wipetower](#turning-off-slicer-wipetower)
  - [How to verify configuration](#how-to-verify-configuration)

*\[This guide is copied directly from the [Happy Hare Slicer Setup](https://github.com/moggieuk/Happy-Hare/wiki/Slicer-Setup) page. Thanks Moggie!\]*

When printing with an MMU you must augment the gcode generated by your slicer to include logic to initialize the MMU, load the initial filament and optionally reset and eject filament at the end of the print. To achive that it is necessary to enable MMU support in your slicer and then edit the custom g-code. While there are many ways to do this, Happy Hare recommends the following pre-packaged macro to take advantage of all the advanced features. Consider this best practice for setut and note the probable need to separate your existing "start_print" macro into two parts.

Make sure the `Expert Options` of your slicer are enabled and go to the Printer Settings tab.

<br>

## #f03c15 #c5f015 #1589F0 Start G-Code

Enter the following (using your own print start macro call) into your "custom start g-code" box:

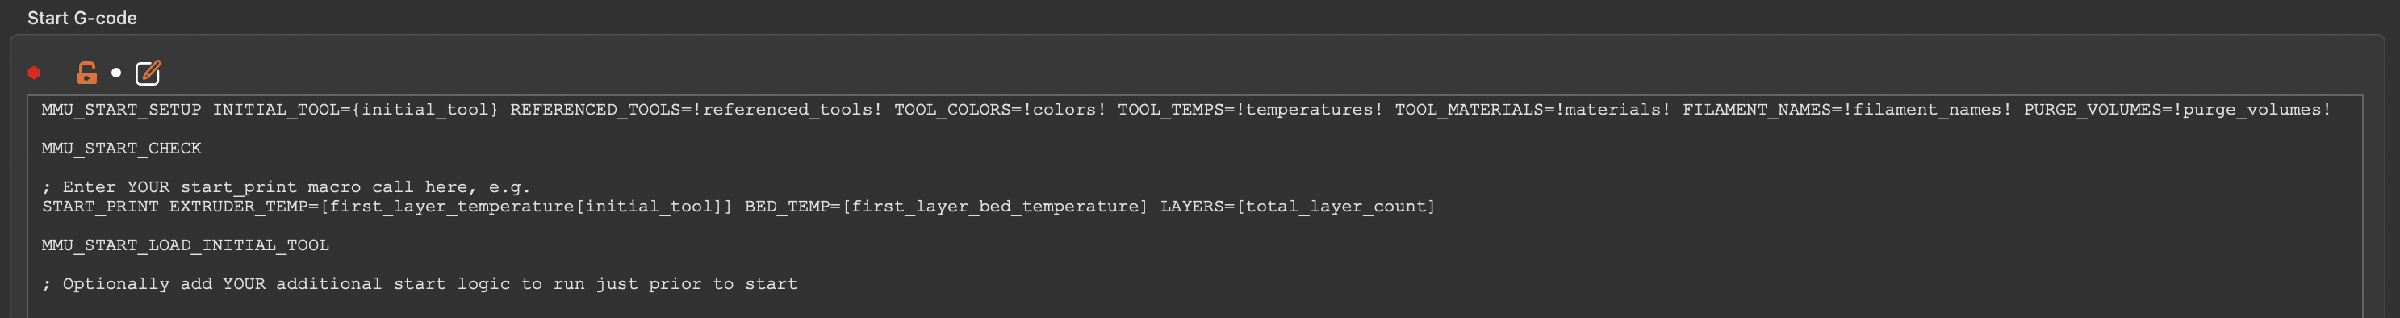
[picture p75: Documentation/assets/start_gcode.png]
Custom Start G-Code
<br>Your `START_PRINT ...` macro is likely to be different from mine! Here is some cut'n'paste text:

```yml
MMU_START_SETUP INITIAL_TOOL={initial_tool} TOTAL_TOOLCHANGES=!total_toolchanges! REFERENCED_TOOLS=!referenced_tools! TOOL_COLORS=!colors! TOOL_TEMPS=!temperatures! TOOL_MATERIALS=!materials! FILAMENT_NAMES=!filament_names! PURGE_VOLUMES=!purge_volumes!
MMU_START_CHECK
; Enter YOUR exist start_print macro call here (minus purging logic because tool may not be loaded yet)
MMU_START_LOAD_INITIAL_TOOL
; Optionally add YOUR additional start logic (like purging) here to run just prior to start
SET_PRINT_STATS_INFO TOTAL_LAYER={total_layer_count} ; For pause at layer functionality and better print stats
```

> [!NOTE]  
> There are two reasons that it is recommended to add these separate 4-5 lines in your slicer:<br>
> - Keeping them as separate gcode macros to enables the print to pause and then continue in the case of an error.  If you bundle everything into a single print start macro then the first opportunity to pause will be at the end of that, potentially long running, macro! (This is particularly accute if using the new klipper pop-up dialogs -- these frustratingly will not be able to be closed until the current macro is complete)
> - You will likely want to separate out any nozzle purging logic you have in your current "start_print" marco and run it AFTER all the MMU checks and loading the initial tool

### Sequence Explained:

#### `1. MMU_START_SETUP`
This is a macro (defined in `mmu_software.cfg`) that is passed information either through slicer "placeholder" variables delimited by `{}` like `{initial_tool}` or through a similar mechanism implemented by Happy Hare's moonraker extension which pre-processes the g-code file when it is uploaded and substitutes `!!` like `!referenced_tools!` that are useful for MMU printing. Unfortunately these placeholders are absent in all popular slicer programs hence the pre-processor extension. Happy Hare's g-code pre-processing is explained in [detail here](https://github.com/moggieuk/Happy-Hare/wiki/Gcode-Preprocessing)

This macro initializes the MMU, establishes whether the print is single or multi-color, detects when the intent is to print bypassing the MMU and then stores this infomation in Happy Hare for the duration of the print in the "Slicer Tool Map". This can be accessed in your own macros through the `printer.mmu.slicer_tool_map` printer variable. E.g.

```yml
   printer.mmu.slicer_tool_map.
      initial_tool: 0          ; Initial tool number expected to be loaded at the beginning of the print
      ; List of all the tools referenced in the print (T0 and T3)
      tools.0.color: ff0000    ; Color in RRGGBB format for T0
      tools.0.material: ABS    ; Material type for T0
      tools.0.temp: 240        ; Extruder temperature for T0
      tools.0.in_use: 1        ; Tool used in print
      tools.3.color: 00e410    ; Color in RRGGBB format for T3
      tools.3.material: ASA    ; Material type for T3
      tools.3.temp: 245        ; Extruder temperature for T3
      tools.3.in_use: 1        ; Tool used in print
      purge_volumes: [[100, 100], [100, 100]] ; NxN matrix of purge volume changing from tool X to tool Y
```

The "Slicer Tool Map" can be displayed on the console at any time during the print by running the `MMU_SLICER_TOOL_MAP` command without any set parameters (optional `DETAIL=1` or `PURGE_MAP=1` or `SPARSE_PURGE_MAP=1` to see purge matrix):<br>
> MMU_SLICER_TOOL_MAP PURGE_MAP=1<br>
```
-------- Slicer MMU Tool Summary ---------
2 color print (Purge volume map loaded)
T0 (Gate 0, ABS, ff0000, 240°C)
T3 (Gate 3, ASA, 00e410, 245°C)
Initial Tool: T0
-------------------------------------------
Purge Volume Map:
To -> T0   T1   T2   T3   T4   T5   T6   T7   T8
T0    -   200  200  200  200  200  200  200  200
T1   200   -   200  200  200  200  200  200  200
T2   200  200   -   200  200  200  200  200  200
T3   200  200  200   -   200  200  200  200  200
T4   200  200  200  200   -   200  200  200  200
T5   200  200  200  200  200   -   200  200  200
T6   200  200  200  200  200  200   -   200  200
T7   200  200  200  200  200  200  200   -   200
T8   200  200  200  200  200  200  200  200   -
```
Note that the `DETAIL=1` flag will also report on tools that are defined in slicer but not defined for current print. Similarly adding `SPARSE_PURGE_MAP=1` can make the purge volumes more readable but showing only referenced tools.

#### `2. MMU_START_CHECK`
This macro uses the "Slicer Tool Map" and performs checks to ensure the MMU is fully ready to print. Currently checks are limited to confirming that filament is available in all the required tools, but in the future it might check that the filaments types the sliced g-code expects match those actually loaded in the MMU (think how the Spoolman integration could be used...)
If this macro fails, the print will pause but not abort or skip the rest of the startup sequence. 

> [!TIP]  
> On failure while in a paused state, you can run this macro by hand to repeat the checks. Simply run `MMU_START_CHECK` without any parameters

#### `3.`START_PRINT...
This is where you put your normal print start macro passing additional slicer placeholders it may require. This macro doesn't need to do anything added for MMU support and will likely home the printer, level the bed and set print temperatures. It shouldn't have logic that assumes the extruder is loaded with filament - activities like purging should be separated out and included later (see step 5).

#### `4. MMU_START_LOAD_INITIAL_TOOL`
This macro will load the initial tool used by the print. No need to pass it any information - it retrieves it from the "Slicer Tool Map" setup earlier

#### `5.` Optional purge logic...
Optionally you can put the parts of your original print start macro that you separated out here. Typically this would be the logic that purges the nozzle, cleans nozzle and prints prime line. This is separated out because you want it to run AFTER the initial tool have been loaded.

<br>

> [!TIP]  
> Did you know the slicer defined extruder colors can be displayed on Mainsail / Fluidd UI next to the Extruder "Tx" buttons (see below). Happy Hare ensures the color information is parsed from the slicers g-code and provided to this user interface.
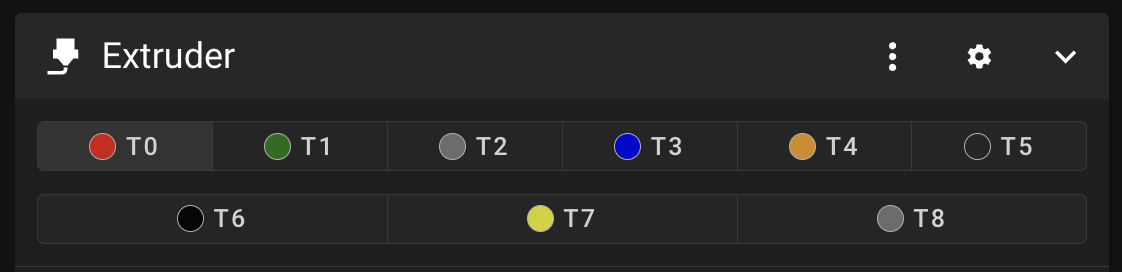
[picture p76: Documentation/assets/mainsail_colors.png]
Mailsail Extruder Colors
> 

<br>

## #f03c15 #c5f015 #1589F0 End G-Code

Ensure this is added in your slicer's "custom end g-code" box:

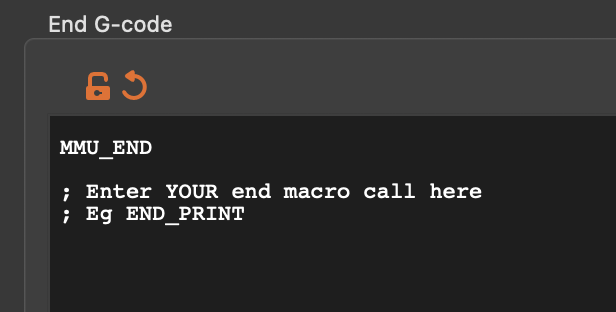
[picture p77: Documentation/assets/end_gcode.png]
End G-Code


```yml
MMU_END
; Optionally enter YOUR print end macro call here
MMU_PRINT_END ; Only required if using Octoprint
```

#### `1. MMU_END`
This is a macro (defined in `mmu_software.cfg`) that finalizes MMU, can print stats, reset any TTG map and eject filament. It is recommended to run this before your existing print end macro which is likely to disable heaters and turn motors off.

#### `2. END_PRINT`
This is where your existing print end macro would be placed

#### `3. MMU_PRINT_END`
This should be the very last g-code executed. When printing from virtual sd-card this isn't techincally necessary (and can be omitted) because Happy Hare will automatically detect the end of print. **It is necessary when printing from Octoprint.**

<br>

## #f03c15 #c5f015 #1589F0 After Layer Change G-Code

The reason for this is to support sequential printing and explained [here](https://github.com/moggieuk/Happy-Hare/wiki/Toolchange-Movement#---z-hop-moves)

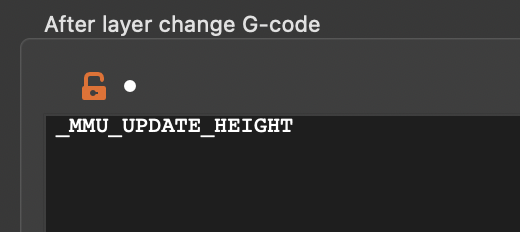
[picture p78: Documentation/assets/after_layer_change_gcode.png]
After Layer Change G-Code


```yml
_MMU_UPDATE_HEIGHT

; If you want enhanced pausing feature with Happy Hare client macros also add this
SET_PRINT_STATS_INFO CURRENT_LAYER={layer_num} ; For pause at layer functionality and better print stats
```

<br>

## #f03c15 #c5f015 #1589F0 Tool Change G-Code

This is likely to be the slicer default, but it is worth checking that the custom tool change g-code is set to this:

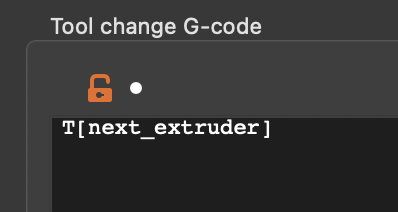
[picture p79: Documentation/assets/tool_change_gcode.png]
Tool Change G-Code


```yml
T[next_extruder]
```

<br>

## #f03c15 #c5f015 #1589F0 Customing MMU Start/End Macros

The recommended macro described here can be customized in `mmu_macro_vars.cfg`. Look for the `_MMU_SOFTWARE_VARS` section (corresponding to `mmu_software.cfg` where the macros are defined) 

```yml
# PRINT START/END ---------------------------------------------------------
#   (base/mmu_software.cfg)
#
[gcode_macro _MMU_SOFTWARE_VARS]
description: Happy Hare optional configuration for print start/end checks
gcode: # Leave empty

# These variables control the behavor of the optional _MMU_INITIALIZE and _MMU_LOAD_INITIAL_TOOL macros
variable_user_pre_initialize_extension      : "G28"     ; Executed at start of _MMU_INITIALIZE. Commonly G28 to home
variable_home_mmu                           : False     ; True/False, Whether to home mmu before print starts
variable_check_gates                        : True      ; True/False, Whether to check filament is loaded in all gates used
variable_load_initial_tool                  : True      ; True/False, Whether to automatically load initial tool

# These variables control the behavor of the optional _MMU_FINALIZE macro
variable_eject_tool                         : True      ; True/False, Whether to eject the tool at the end of the print
variable_reset_ttg                          : False     ; True/False, Whether reset TTG map at end of print
variable_dump_stats                         : True      ; True/False, Whether to display print stats at end of print
```

<br>

## #f03c15 #c5f015 #1589F0 MMU Error Dialog

When Happy Hare detects an error, even during print start it will pause the print allowing you to fix and then resume. If the option `show_error_dialog: 1` is set in `mmu_parameters.cfg` a pop-up dialog will be displayed on Mailsail/Fluidd/KlipperScreen providing you options through the UI. If it is occurs during these startup macros there will also be an option to abort the print. The abort option will disappear during the print. To disable the popup, set `show_error_dialog: 0`

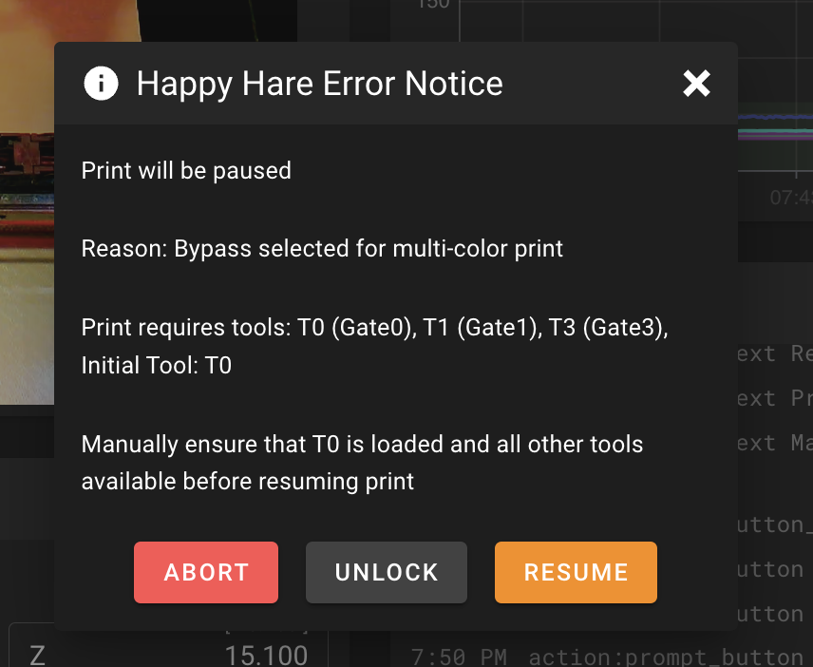
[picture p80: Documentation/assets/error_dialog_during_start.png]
Error Dialog


> [!IMPORTANT]  
> If you are writing your own startup macros beware of the earlier note because the use of a popup dialog can make it seem as though your printer is locked up for long running macros

<br>

## #f03c15 #c5f015 #1589F0 Slicer Tip Forming

The most important part of MMU printing is understanding how to configure your slicer for "single extruder multi material".  Because each slicer is different this is beyond the scope this documentation.  That said, the common slicers: Prusaslicer, Superslicer and Orcaslicer all have similar interfaces and there are a couple of settings you need to be aware of in deciding between what is performed by Happy Hare (the MMU "firmware") and the slicer.

### Turning off slicer tip forming
The first thing that has to happen on a tool change is to prepare the tip of the filament being removed from the extruder. The simplist and recommend approach is to disable the tip creation process in the slicer and allow Happy Hare to do this. The reason is Happy Hare will have to do this while not actively printing anyway - so why configure what will likely be the most furstrating part of your journey in two places.

Slicers have some quirks and don't make it very straighforward to turn off as you would expect. Instead you need to configure in a number of different areas.  This screenshots shown here are for Prusaslicer but Superslicer and Orcaslicer are very similar.

The first place is a setting like this on the `printer settings` tab.  This disables the primary retract/extrude oscillation that is the bulk of the tip forming and cooling movement.

> [!NOTE]  
> Whilst it is logical to zero all these settings out, Older versions of Prusaslicer (v2.5 - v2.7) at least has bug that will insert illegal `G1 F0` commands if all the fields are exactly 0.  For these versions only use a tiny value for the cooling tube length, like "0.01" instead.
> <br>
> **With PrusaSlicer v2.8 and above please use a value of exactly 0.**

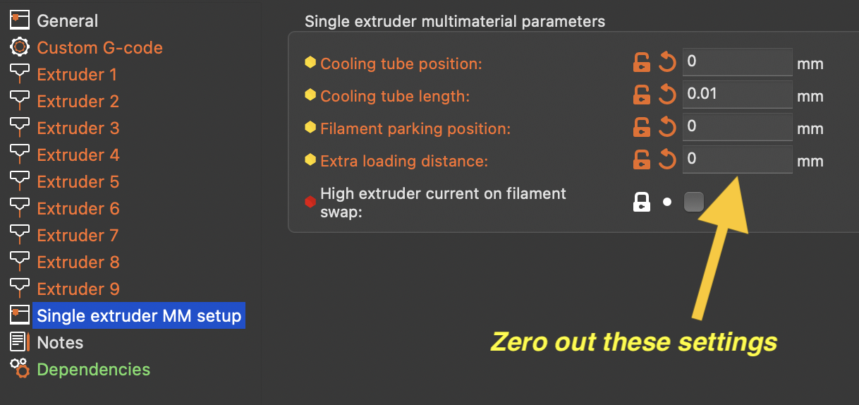
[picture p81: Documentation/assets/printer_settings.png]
Slicer printer settings


Working in conjunction with the above and found on the `filament settings` tab is this area where you should zero out all all movement speeds and distances.  Leave only the timing inputs that you can tune once you know the average loading and unloading time for your particular MMU.

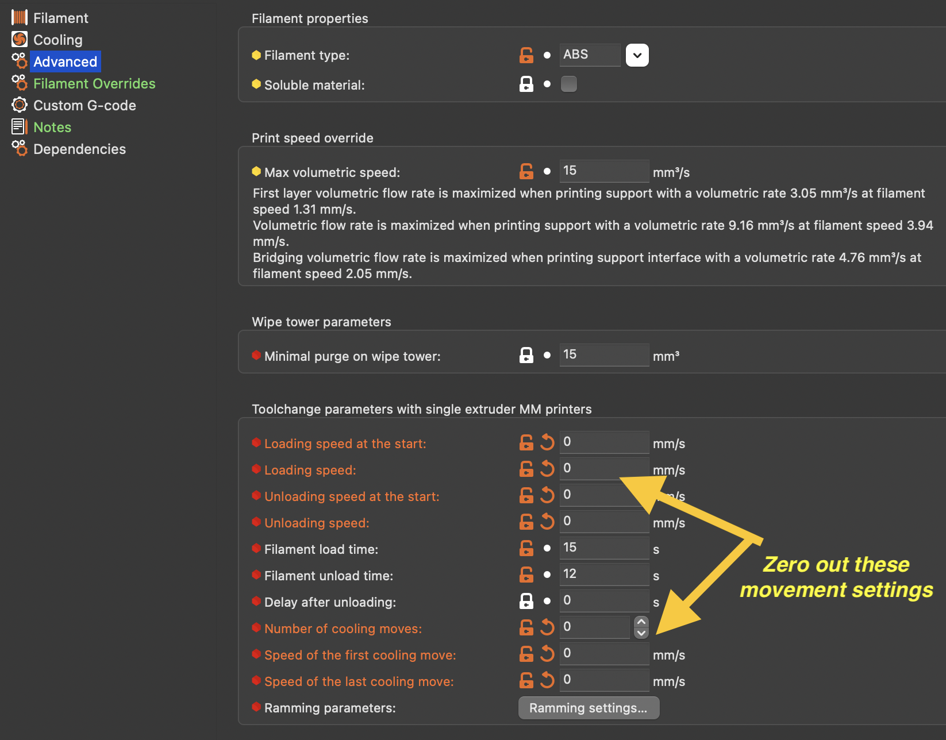
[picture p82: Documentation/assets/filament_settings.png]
Slicer filament settings


The next setting must be configure on each of your extruders.  This turns off an initial retraction and subsequent extrude that will leave blobs on your wipetower.  The reason to turn this off is that Happy Hare will correctly load the filament exatly to the nozzle and additonal extrusion will cause a blob.

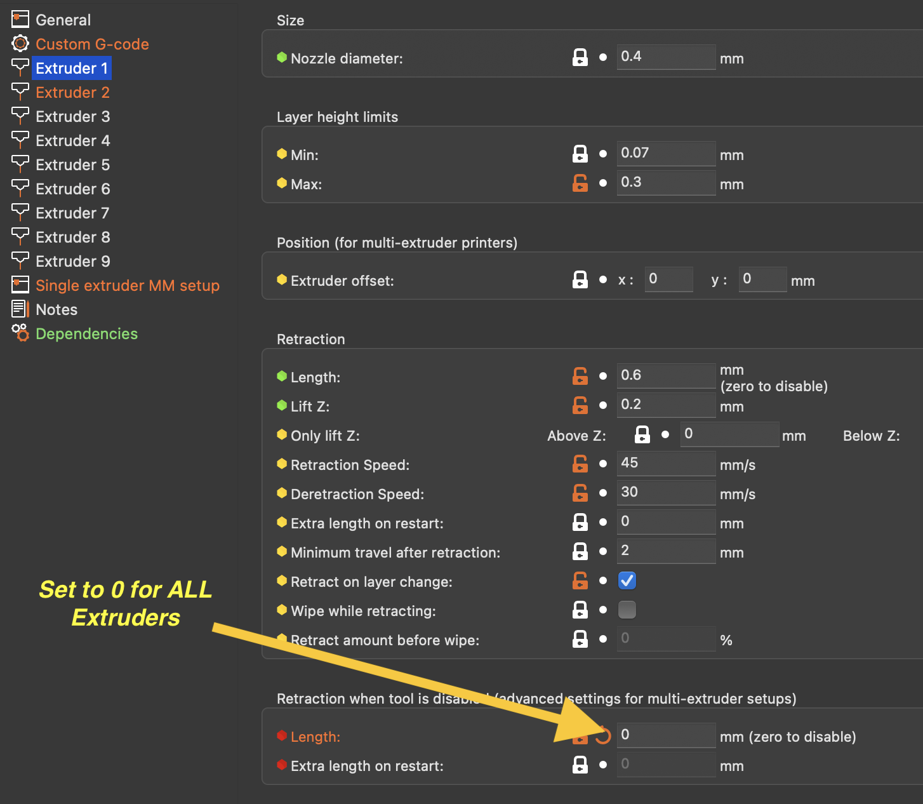
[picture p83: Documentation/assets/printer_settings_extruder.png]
Slicer printer settings per extruder


Unless you have a sepcialized purge system (documented later) you will want the slicer to manage a wipe tower used to purge out the remains of the previous filament.  To do this, make sure this option is enabled (it usually is by default):

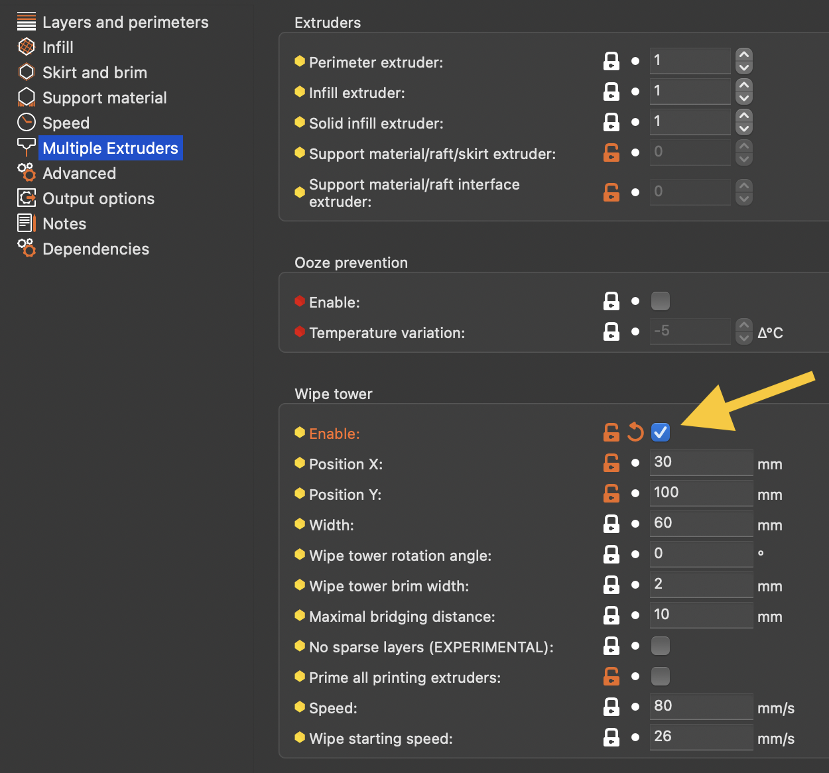
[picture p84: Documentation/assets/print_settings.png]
Slicer print settings


> [!NOTE]  
> If you use SuperSlicer, be sure to turn off Skinnydip:
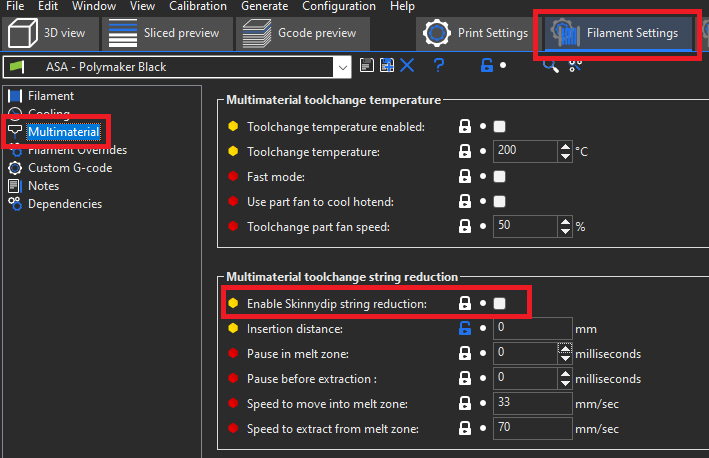
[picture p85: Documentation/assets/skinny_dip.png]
Skinnydip disabling
> <br><br>
> It's probably also a good idea to zero out the distances below.
> Doing this prevents Superslicer from pushing out a blob of filament before cutting the tip.

### Turning off slicer wipetower
To switch to a custom purge system you need only to untoggle the `enable wipetower` option.  All tip forming settings remain the same.

### How to verify configuration
To be sure you have your slicer setup correctly (not doing any tip shaping for example), examine the g-code it creates. Seach for a toolchange section -- this will either have `Tx` commands or will have been parsed to `MMU_CHANGE_TOOL` by the Happy Hare moonraker extension depending on where you are examining the file. Anyway, look at the g-code around the toolchange. It should be clean like this:
```
;--------------------
; CP TOOLCHANGE START
; toolchange #1
; material : ASA -> ASA
;--------------------
; WIPE_TOWER_START
M220 S100
; CP TOOLCHANGE UNLOAD
;WIDTH:0.6
;WIDTH:0.5
M104 S260
; Cooling park
G4 S0
; filament end gcode 
T0
M106 S255
SET_PRESSURE_ADVANCE ADVANCE=0.025 SMOOTH_TIME=0.001 EXTRUDER=extruder
```
And not like this (this is simply one example, many other are more obvious):
```
;--------------------
; CP TOOLCHANGE START
; toolchange #2
; material : ASA -> ASA
;--------------------
; WIPE_TOWER_START
M220 S100
; CP TOOLCHANGE UNLOAD
;WIDTH:0.6
;WIDTH:0.5
; Retract(unload)
G1  X204.504 Y102.283 E-15.0000
G1 E10.4965
G1 E2.9990
G1 E1.4995
; Cooling park
G1 E0.0050 F2000
G4 S0
; filament end gcode 
T2
M106 S255
SET_PRESSURE_ADVANCE ADVANCE=0.025 SMOOTH_TIME=0.001 EXTRUDER=extruder
```
Can you see the unwanted 15mm retraction?  That is the first part of tip creation and you don't want the slicer to do this if you have elected to always let Happy Hare do it.

I wish slicers made it easy to toggle tip forming on/off but unfortunately that is not the case, hence the need to inspect an example generated file to verify it is as expected.

### ERCF Setup Steps:
- [Flashing Your Local MCU](https://github.com/Enraged-Rabbit-Community/ERCFv2.5/blob/main/Documentation/Flashing-Local-MCU.md)
- [Installing Happy Hare](https://github.com/Enraged-Rabbit-Community/ERCFv2.5/blob/main/Documentation/Installing-Happy-Hare.md)
- [Happy Hare Configuration](https://github.com/Enraged-Rabbit-Community/ERCFv2.5/blob/main/Documentation/Happy-Hare-Configuration.md)
- [Hardware Configuration Checks](https://github.com/Enraged-Rabbit-Community/ERCFv2.5/blob/main/Documentation/Hardware-configuration-checks.md)
- [Hardware Calibration](https://github.com/Enraged-Rabbit-Community/ERCFv2.5/blob/main/Documentation/Hardware-Calibration.md)
- [Toolhead Distances](https://github.com/Enraged-Rabbit-Community/ERCFv2.5/blob/main/Documentation/Toolhead-Distances.md)
- [Installing KlipperScreen Happy Hare](https://github.com/Enraged-Rabbit-Community/ERCFv2.5/blob/main/Documentation/Installing-KlipperScreen.md)
- Slicer Setup
- [Further Mods to Consider](https://github.com/Enraged-Rabbit-Community/ERCFv2.5/blob/main/Documentation/Further-Mods.md)

#### Even more Happy Hare info can be found at:
- [Happy Hare Wiki](https://github.com/moggieuk/Happy-Hare/wiki)

### Additional Happy Hare Information:
- [Tip Forming and Purging](https://github.com/moggieuk/Happy-Hare/wiki/Tip-Forming-and-Purging)
- [Toolchange Movement](https://github.com/moggieuk/Happy-Hare/wiki/Toolchange-Movement)

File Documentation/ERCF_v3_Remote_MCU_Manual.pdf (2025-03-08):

LOCAL MCU VS REMOTE MCU
When we say “local MCU” we mean a “buddy board” or other dedicated MCU that will be mounted near the ERCF. Examples include the BTT MMB (the preferred option) and the EASY BRD. Skip to page 24 if you’re using a local MCU.

When we say “remote MCU” we mean the dedicated MCU(s) for your printer. It is unusual to have enough spare motor, servo, and endstop ports to run an ERCF unless you’re using a dual SKR board setup, but if that’s you, then you can save some money on the buddy board by using this option.

PREPARING THE WIRES FOR REMOTE MCU
For an ease of installation, it is recommended to prepare the wiring before assembly. There are two wire looms to do:
- One that goes from the connector plate to the selector motor
- One that goes from the connector plate to all the other components, namely the endstop, the servo and the encoder

WIRING (REMOTE MCU)

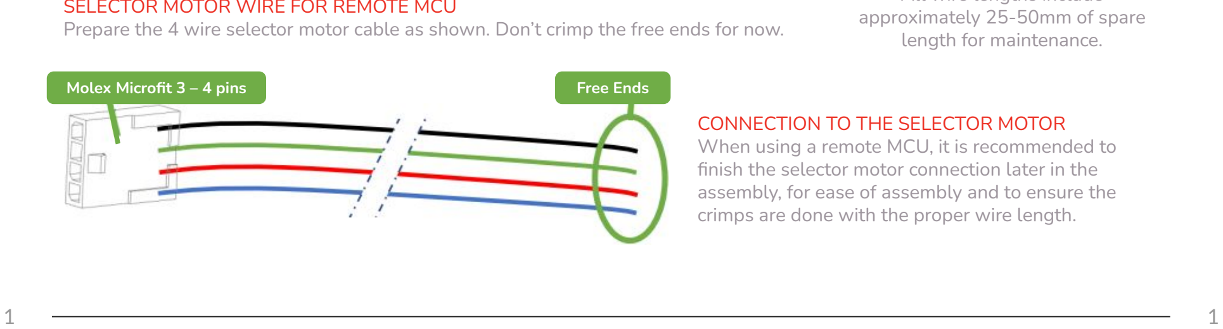
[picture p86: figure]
Molex Microfit 3 – 4 pins; Free Ends; CONNECTION TO THE SELECTOR MOTOR; approximately 25-50mm of spare length for maintenance.

When using a remote MCU, it is recommended to finish the selector motor connection later in the assembly, for ease of assembly and to ensure the crimps are done with the proper wire length.

SELECTOR MOTOR WIRE FOR REMOTE MCU
Prepare the 4 wire selector motor cable as shown. Don’t crimp the free ends for now.

SELECTOR MOTOR WIRE

Channels | Selector Motor Wire Length (mm)
N 175 + 25N
4 275
5 300
6 325
7 350
8 375
9 400
10 425
11 450
12 475
13 500
14 525
15 550

Wire Length Chart for remote MCU

All wire lengths include

GEAR MOTOR WIRE
Trim your Gear Motor wires to 85mm, then crimp and add the 4-pin Molex Microfit connector. That’s it!

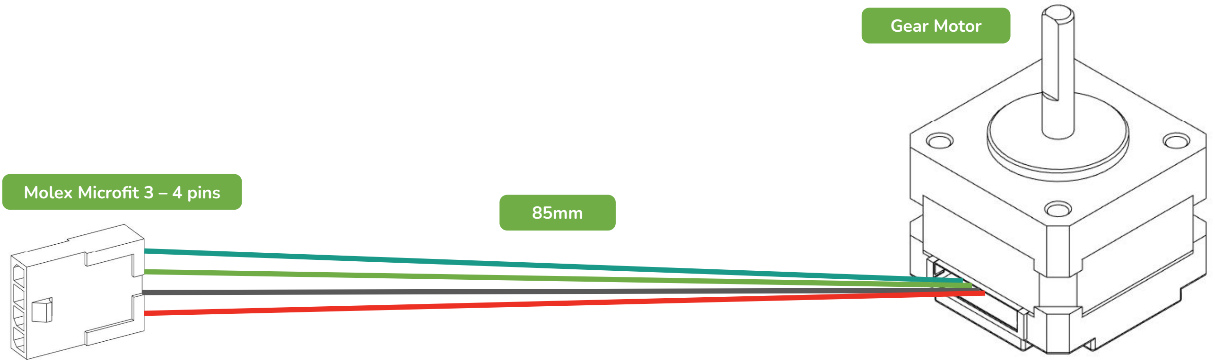
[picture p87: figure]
Molex Microfit 3 – 4 pins; Gear Motor

2 | 2

WIRING (REMOTE MCU)
GEAR MOTOR WIRE

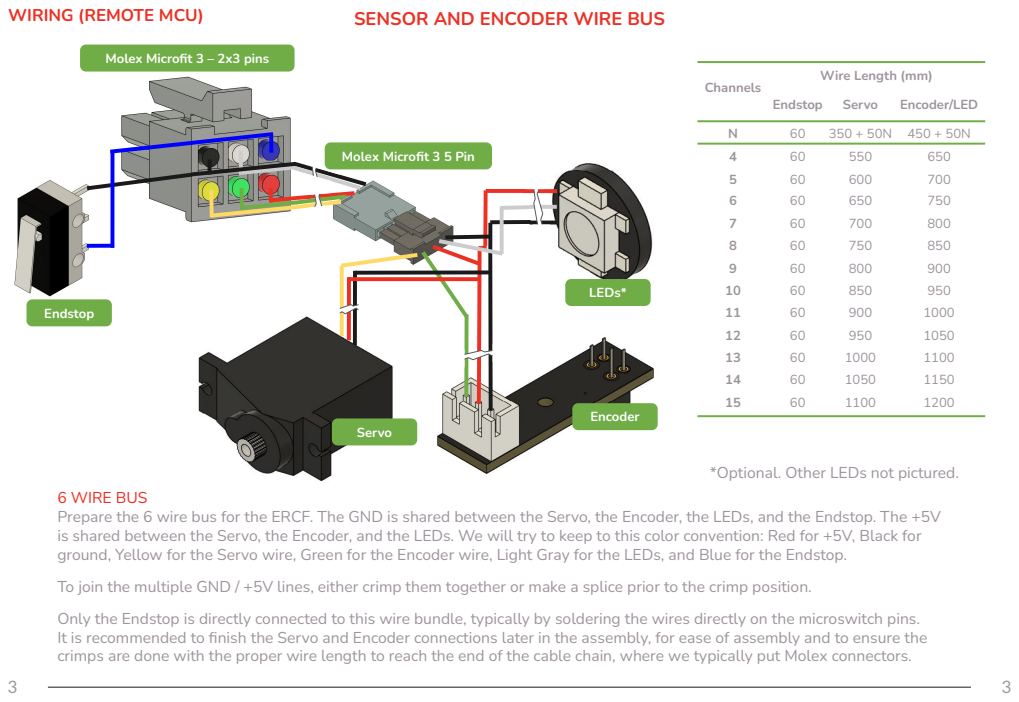
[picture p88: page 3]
Servo; Encoder; Endstop; Channels; Endstop Servo; Encoder/LED; LEDs*

WIRING (REMOTE MCU)

SENSOR AND ENCODER WIRE BUS

Molex Microfit 3 – 2x3 pins

Wire Length (mm)

Molex Microfit 3 5 Pin

*Optional. Other LEDs not pictured.

6 WIRE BUS
Prepare the 6 wire bus for the ERCF. The GND is shared between the Servo, the Encoder, the LEDs, and the Endstop. The +5V
is shared between the Servo, the Encoder, and the LEDs. We will try to keep to this color convention: Red for +5V, Black for
ground, Yellow for the Servo wire, Green for the Encoder wire, Light Gray for the LEDs, and Blue for the Endstop.
To join the multiple GND / +5V lines, either crimp them together or make a splice prior to the crimp position.
Only the Endstop is directly connected to this wire bundle, typically by soldering the wires directly on the microswitch pins.
It is recommended to finish the Servo and Encoder connections later in the assembly, for ease of assembly and to ensure the
crimps are done with the proper wire length to reach the end of the cable chain, where we typically put Molex connectors.

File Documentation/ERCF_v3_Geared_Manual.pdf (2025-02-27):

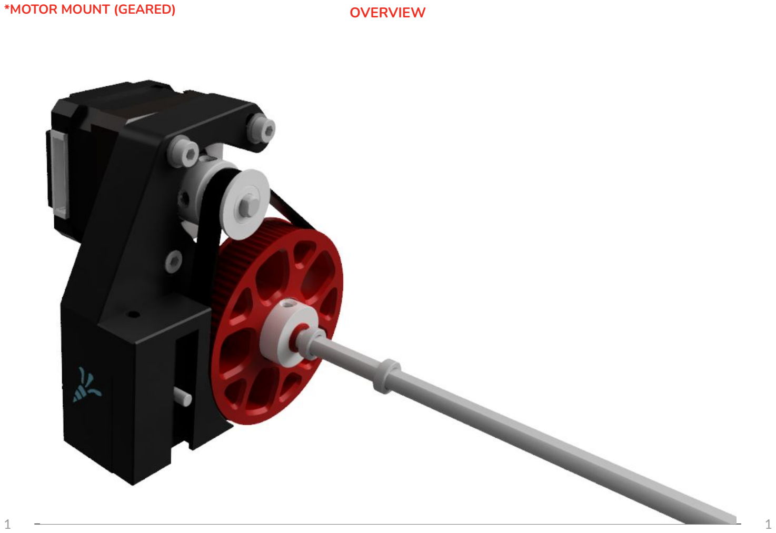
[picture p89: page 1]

*MOTOR MOUNT (GEARED) | OVERVIEW

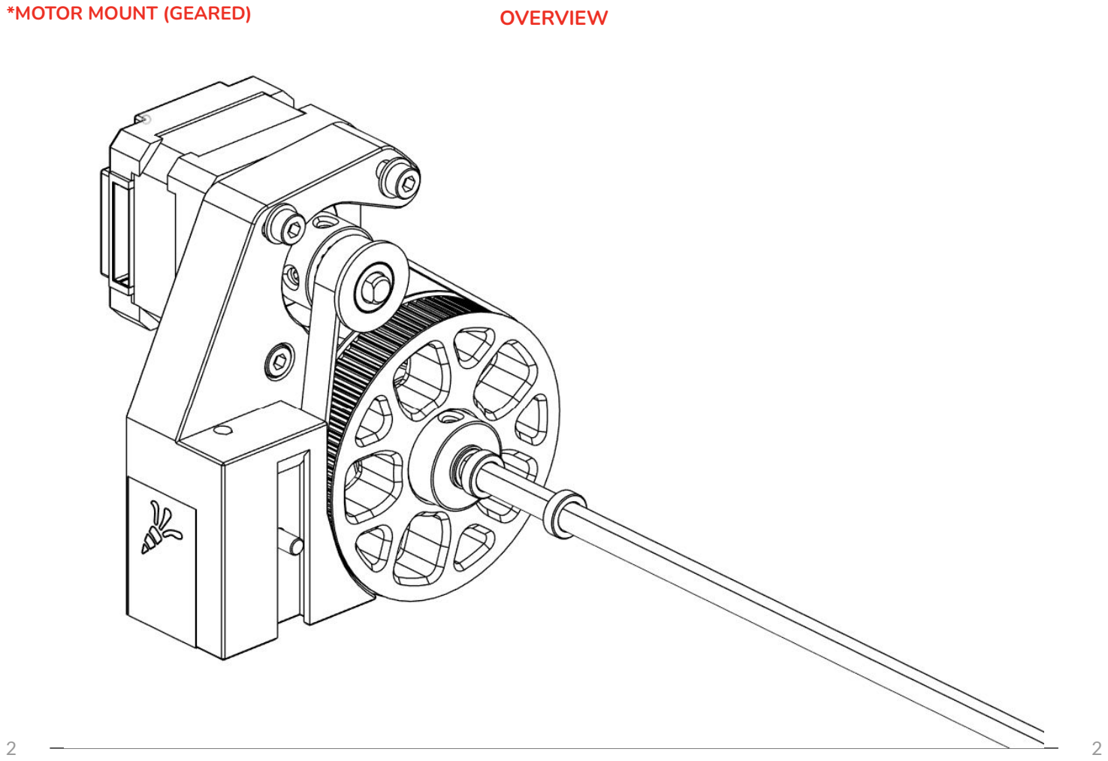
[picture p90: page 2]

*MOTOR MOUNT (GEARED) | OVERVIEW

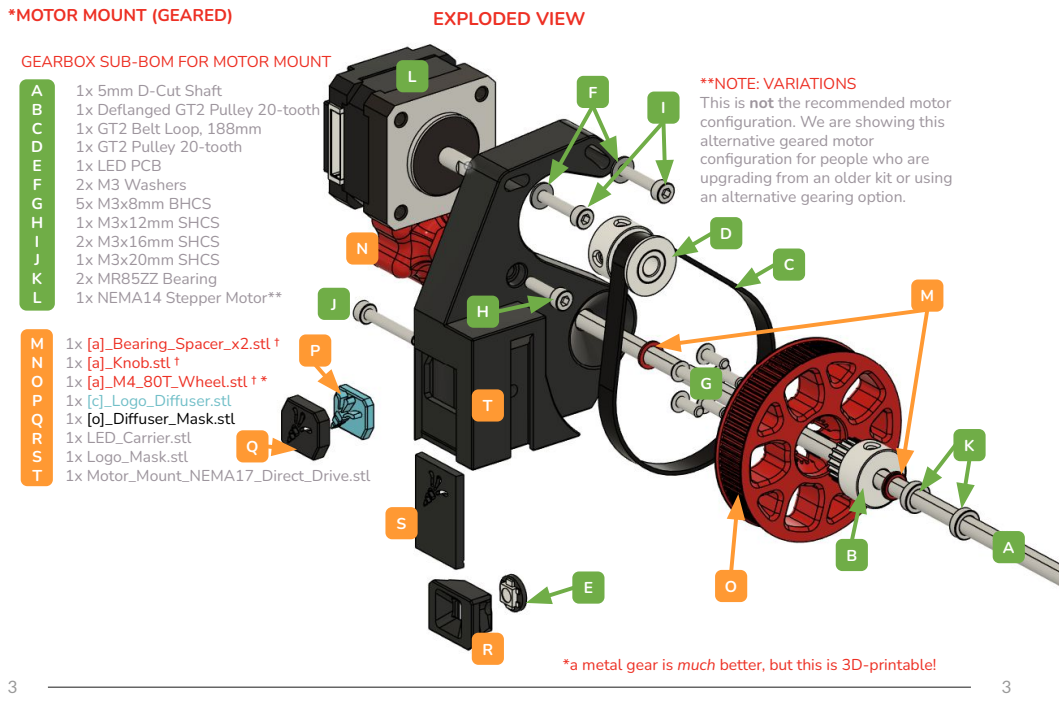
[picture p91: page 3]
1x 5mm D-Cut Shaft 1x Deflanged GT2 Pulley 20-tooth 1x GT2 Belt Loop, 188mm 1x GT2 Pulley 20-tooth 1x LED PCB 2x M3 Washers 5x M3x8mm BHCS 1x M3x12mm SHCS 2x M3x16mm SHCS 1x M3x20mm SHCS 2x MR85ZZ Bearing 1x NEMA14 Stepper Motor**; 1x [a]_Bearing_Spacer_x2.stl † 1x [a]_Knob.stl † 1x [a]_M4_80T_Wheel.stl † * 1x [c]_Logo_Diffuser.stl 1x [o]_Diffuser_Mask.stl 1x LED_Carrier.stl 1x Logo_Mask.stl 1x Motor_Mount_NEMA17_Direct_Drive.stl

*MOTOR MOUNT (GEARED) | EXPLODED VIEW

GEARBOX SUB-BOM FOR MOTOR MOUNT

**NOTE: VARIATIONS
This is not the recommended motor
configuration. We are showing this
alternative geared motor
configuration for people who are
upgrading from an older kit or using
an alternative gearing option.

*a metal gear is much better, but this is 3D-printable!

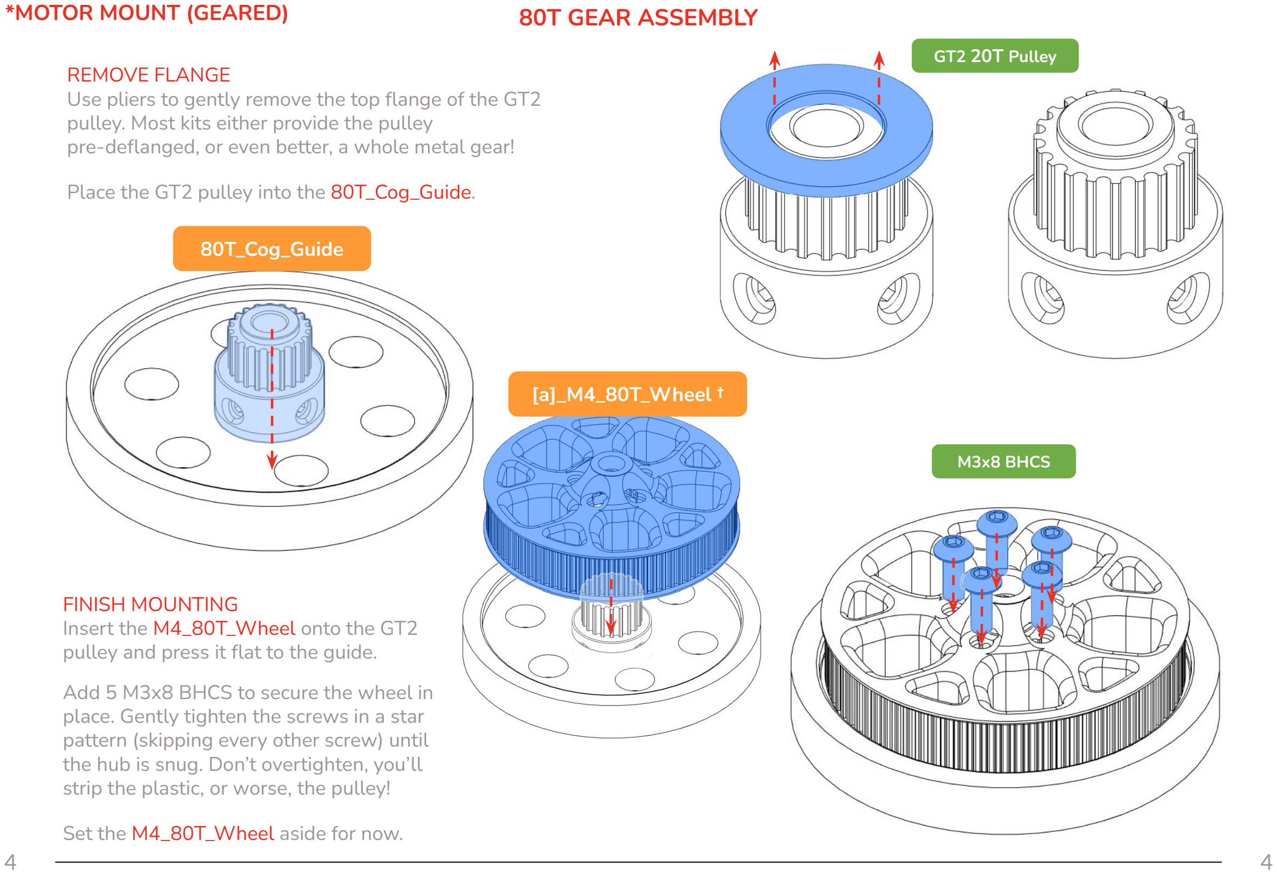
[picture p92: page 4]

*MOTOR MOUNT (GEARED) | 80T GEAR ASSEMBLY

REMOVE FLANGE Use pliers to gently remove the top flange of the GT2 pulley. Most kits either provide the pulley pre-deflanged, or even better, a whole metal gear! Place the GT2 pulley into the 80T_Cog_Guide.

M3x8 BHCS

GT2 20T Pulley

[a]_M4_80T_Wheel †

FINISH MOUNTING
Insert the M4_80T_Wheel onto the GT2 pulley and press it flat to the guide.
Add 5 M3x8 BHCS to secure the wheel in place. Gently tighten the screws in a star pattern (skipping every other screw) until the hub is snug. Don’t overtighten, you’ll strip the plastic, or worse, the pulley!

Set the M4_80T_Wheel aside for now.

80T_Cog_Guide

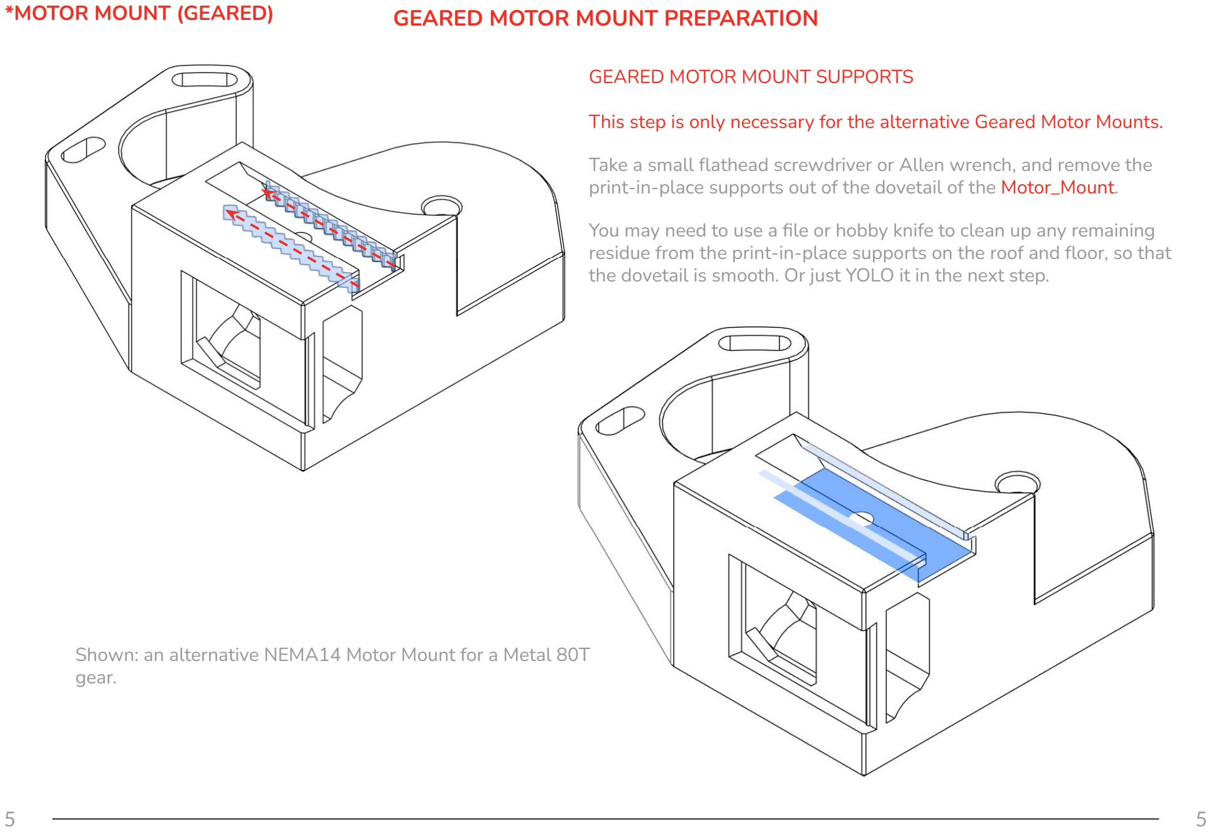
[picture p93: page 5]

GEARED MOTOR MOUNT SUPPORTS

This step is only necessary for the alternative Geared Motor Mounts.

Take a small flathead screwdriver or Allen wrench, and remove the print-in-place supports out of the dovetail of the Motor_Mount.

You may need to use a file or hobby knife to clean up any remaining residue from the print-in-place supports on the roof and floor, so that the dovetail is smooth. Or just YOLO it in the next step.

*MOTOR MOUNT (GEARED) | GEARED MOTOR MOUNT PREPARATION

Shown: an alternative NEMA14 Motor Mount for a Metal 80T gear.

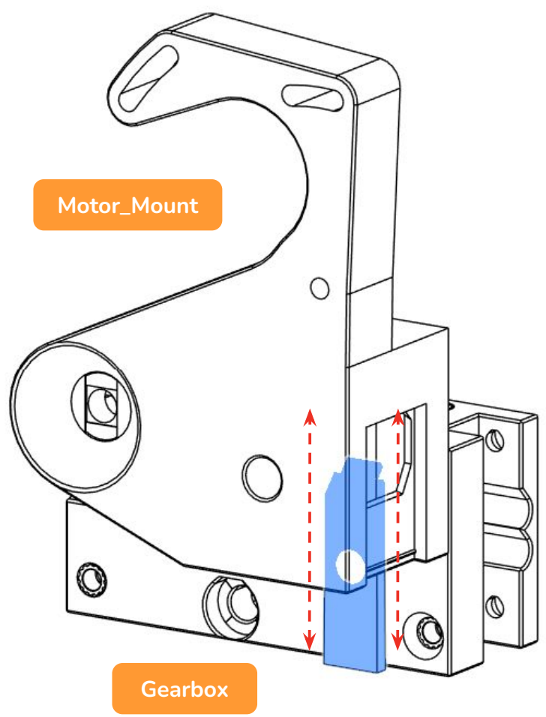
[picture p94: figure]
Gearbox; Motor_Mount

2.1 MOTOR MOUNT MESHING
Take your choice of Motor_Mount and carefully mate the dovetail on the Gearbox to the slot in the Motor_Mount. If it is a tight fit, take sandpaper, a file, or a hobby knife to the parts that are rubbing so that it meshes and unmeshes without too much force. We want this dovetail to mesh with little effort so that later assembly steps are easy.

If the fit between these parts is too tight to put together or pull apart, it’s a good sign that you either need to reprint the parts, or possibly tune your printer more, especially the Extrusion Multiplier. The parts are designed to fit together and come apart with your hands alone, and without straining. It is normal for the first 3-4 times fitting together to be “sticky,” but simply meshing and remeshing the dovetail several times should smooth things out. It is also normal for the area around the dovetail to wear!

Unmesh and set aside the Motor_Mount for now.

Shown: an alternative NEMA17 Motor Mount for a Metal 60T gear.

*MOTOR MOUNT (GEARED) | GEARBOX PREPARATION

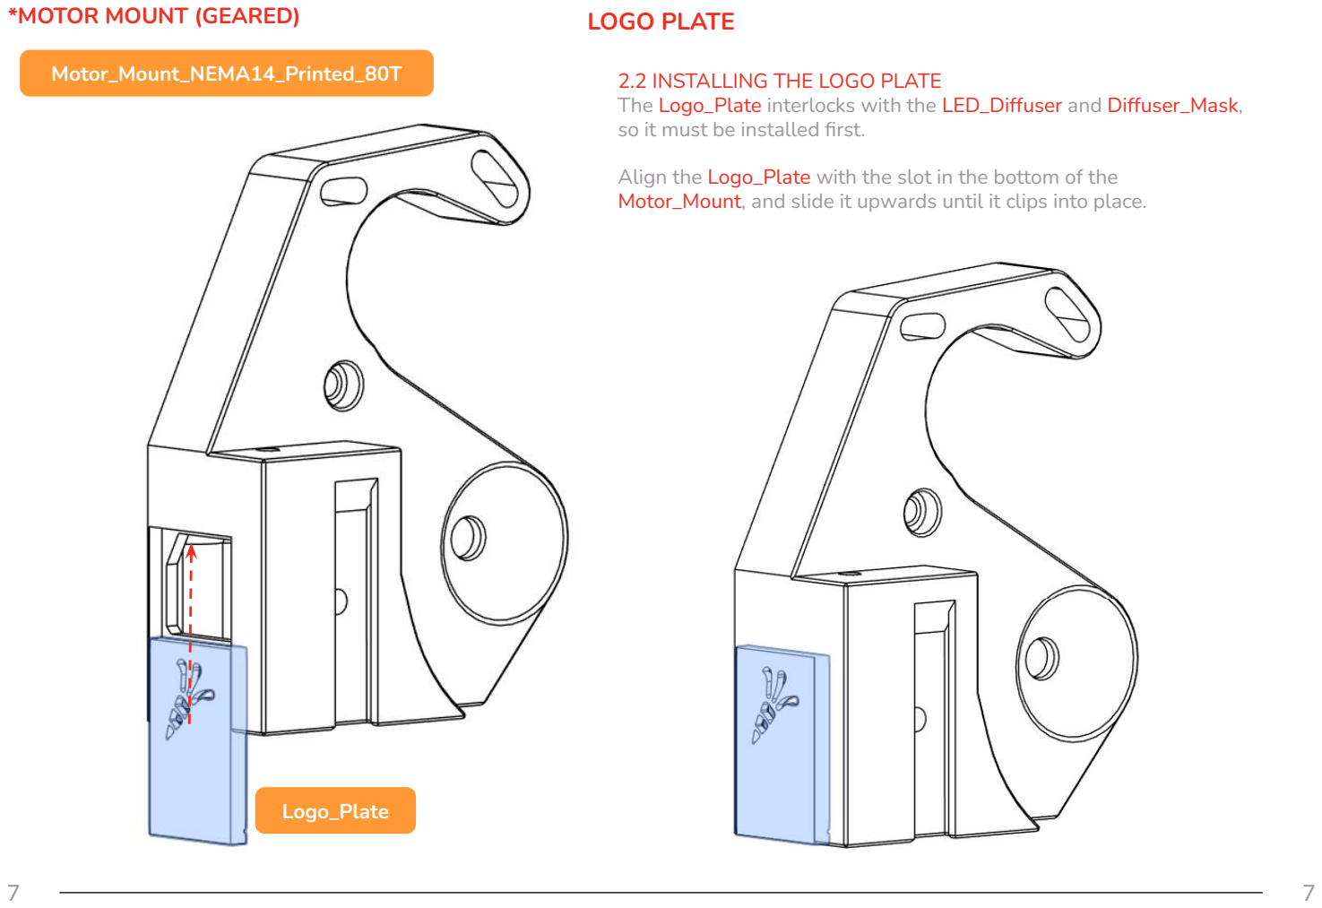
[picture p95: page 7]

*MOTOR MOUNT (GEARED) | LOGO PLATE
| 2.2 INSTALLING THE LOGO PLATE The Logo_Plate interlocks with the LED_Diffuser and Diffuser_Mask, so it must be installed first. Align the Logo_Plate with the slot in the bottom of the Motor_Mount, and slide it upwards until it clips into place.

Motor_Mount_NEMA14_Printed_80T

Logo_Plate

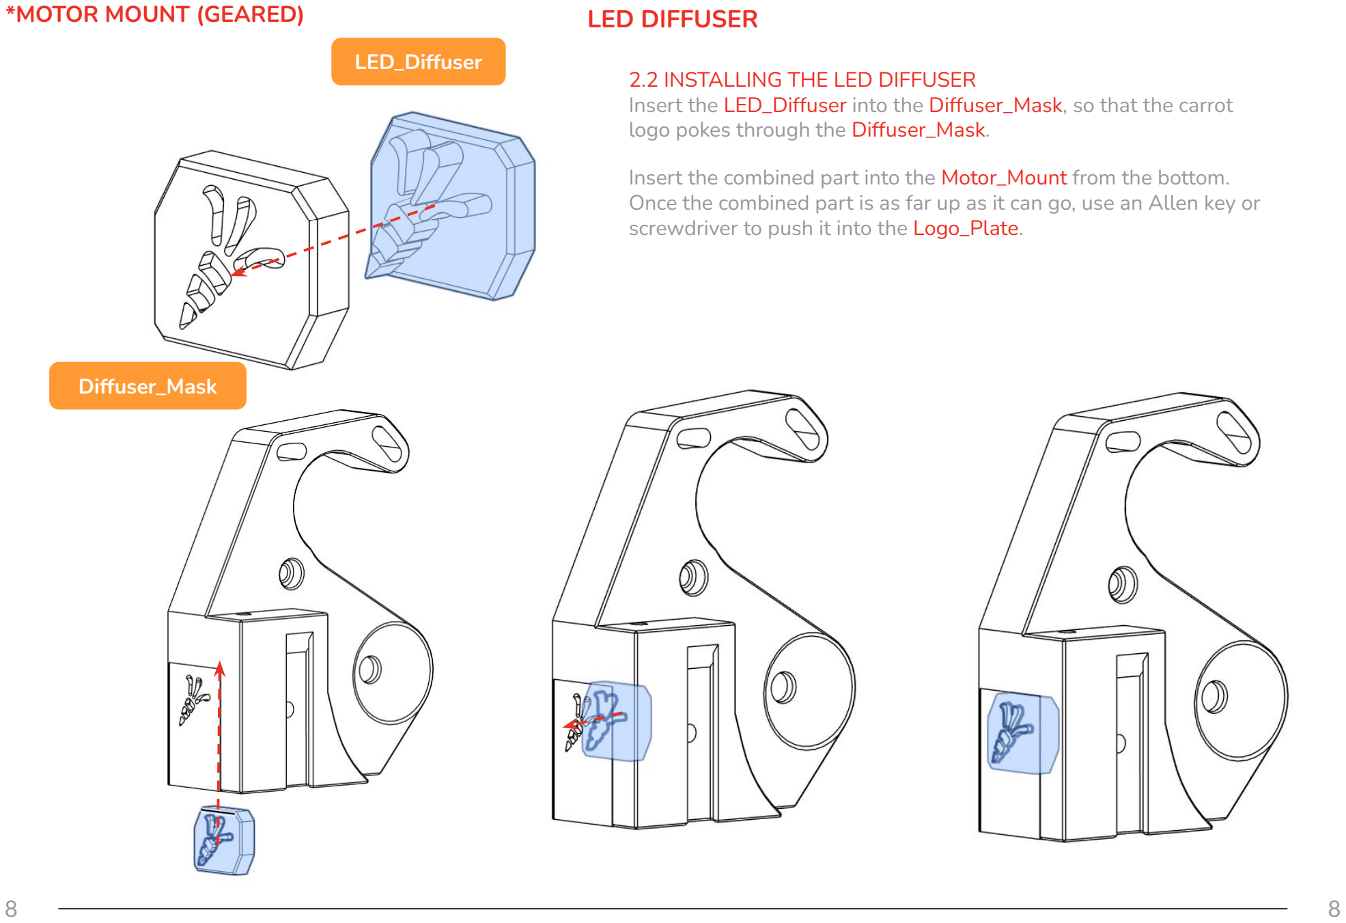
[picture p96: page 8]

*MOTOR MOUNT (GEARED) | LED DIFFUSER
| 2.2 INSTALLING THE LED DIFFUSER Insert the LED_Diffuser into the Diffuser_Mask, so that the carrot logo pokes through the Diffuser_Mask. Insert the combined part into the Motor_Mount from the bottom. Once the combined part is as far up as it can go, use an Allen key or screwdriver to push it into the Logo_Plate.

Diffuser_Mask

LED_Diffuser

*MOTOR MOUNT (GEARED)

2.2 INSTALLING THE LED CARRIER
Insert the LED PCB into the LED_Carrier, so that the edges of the PCB clip into the LED_Carrier. Check the front of the LED_Carrier ro make sure the LED is aligned with the window. The wires are omitted from the images for clarity.

Insert the combined part into the Motor_Mount from the bottom. Use an Allen key or screwdriver to push the combined part up as far as it can go.

If you need to recover the LED for any reason, insert an Allen key into the hole in the roof of the Motor_Mount to push the LED_Carrier back out of the bottom.

LED CARRIER

LED_Carrier

LED PCB

MOTOR VARIATIONS
While the NEMA 17 motor is what is called for in the BOM, we also support NEMA 14 motors for those who are sourcing their own parts or upgrading from a previous version. NEMA 17 motors tend to have more torque but need to run at lower speeds compared to NEMA 14 motors, so NEMA 17 motors are preferred.

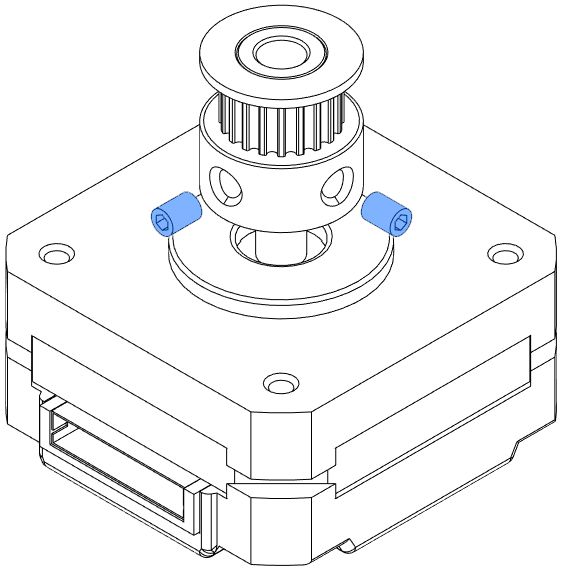
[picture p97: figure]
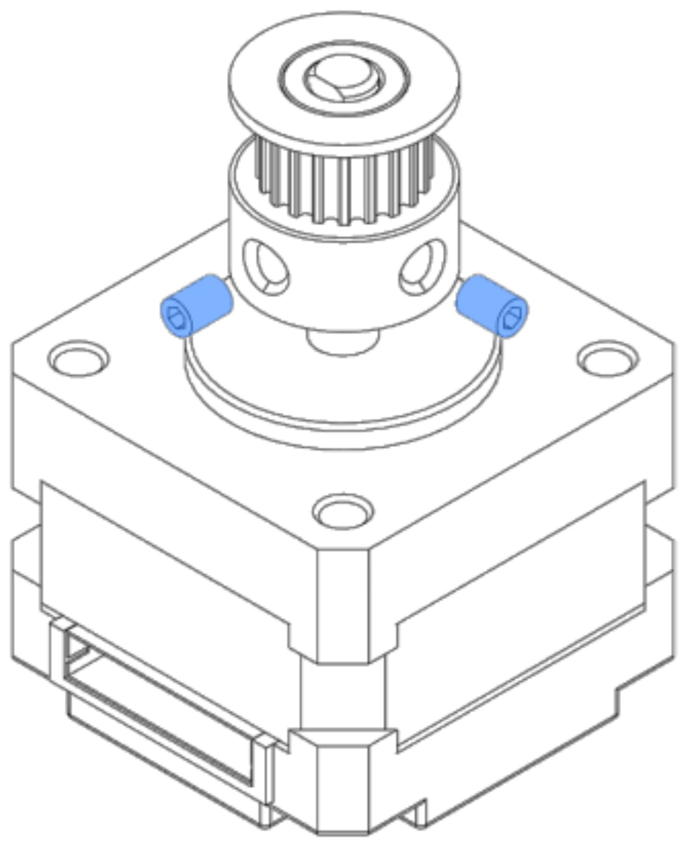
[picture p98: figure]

SET SCREWS
Insert both M3 set screws and use thread locker on them.

Use the appropriate pulley tool to install the pulley at the correct height

*MOTOR MOUNT (GEARED)
MOTOR PREPARATION

on the motor shaft.; PULLEY HEIGHT Use the Pulley_Tool_NEMA17 † to set the correct height of the GT2 20T gear.; If you are using a NEMA 17 motor for the gear axis, assembly is the same but you’ll need to use Pulley_Tool_NEMA14 † and print a different Motor Arm to mount it.; Pulley_Tool_NEMA14 †; Pulley_Tool_NEMA17 †

INSTALLING THE MOTOR
Align the motor to the Motor_Mount with the wires or connector facing left. Start by adding the M3x12mm bolt. Leave the bolt loose enough to use as a hinge.

Next add the M3x16 bolts, adding an M3 washer to each. Leave these loose enough to allow the motor to rotate easily.

*MOTOR MOUNT (GEARED)

MOTOR WIRES
Make sure the wires of the motor come out on this side.
M3x12 SHCS | M3x16 SHCS

M3 Washers

MOTOR MOUNT

Motor_Mount_*

NEMA 14 / 17 Motor

ALTERNATIVE MOTOR MOUNTS
If you look in the User Mods on Github, there is a version for every combination of: Motor type (NEMA 14 and NEMA 17), Gear type (Printed and metal), and gear ratio (gears with 60 teeth and 80 teeth). Assembly uses identical parts.

*MOTOR MOUNT (GEARED) | DRIVE SHAFT AND KNOB

2.3 INSTALLING THE KNOB; Knob †; 5mm D-Cut Shaft; Channels; D-Cut Rod Length (mm)

Insert the 5mm D-cut shaft into the Knob. You may want to use a hammer on the Knob to ensure a snug fit. You don’t want the Knob to come off later!

*MOTOR MOUNT (GEARED) | DRIVE SHAFT ASSEMBLY

2.3 INSTALLING THE DRIVE SHAFT
Insert the 5mm D-cut shaft plus
Knob through the Motor_Mount.

If your D-Cut Shaft is rough or at-spec (4.98-5.00mm), it will be difficult to insert and move the bearings. It is important that we be able to move the shaft along its axis during assembly, so if this is a problem for you, this must be addressed.

For many D-cut shafts, degreasing them with your favorite household cleaner can make the difference between a too-tight fit and a snug fit. If that doesn’t work, follow up with a light-duty abrasive pad.

If you still find that your D-Cut Shaft is too tight on the bearings, take a high-grit sandpaper (at least 300 grit) and sand the shaft. Use a light oil, wear gloves and take appropriate precautions while sanding. You barely want to take any material away at all.

ADDING THE GEAR
Turn the Motor_Mount assembly on its’ side so that the Drive Shaft points up in the air. Add the following parts:
-Bearing_Spacer_x2 (flat side up) -M4_80T_Wheel (screw side down) -Bearing_Spacer_x2 (flat side down) -MR85ZZ Bearing
-MR85ZZ Bearing


*MOTOR MOUNT (GEARED) | DRIVE SHAFT ASSEMBLY

PREP TO ADD THE BELT LOOP
Twist the motor clockwise so that the GT2 Pulley is as close to the M4_80T_Wheel as possible.

2.3 SNUG UP THE GEAR
Push the M4_80T_Wheel to the end of its’ travel, making sure the Knob is snug against the Motor_Mount. Make sure that the Bearing_Spacer_x2 is against the metal pulley part of the M4_80T_Wheel.
Leave some space between the two MR85ZZ bearings.
Metal wheels do not use the Bearing_Spacer_x2, they are only for the printed gears.


*MOTOR MOUNT (GEARED) | DRIVE SHAFT ASSEMBLY

2.3 ADD THE BELT LOOP
Add the 188mm GT2 belt loop to the M4_80T_Wheel.
It is usually easiest to start by putting the belt loop on
the gear first, then the motor pulley.
With the belt installed, lightly twist the motor counter-clockwise to tension the belt loop. Then snug the screws that mount the motor. Do not tighten them yet - we will adjust the belt tension soon. We just need the motor to stay in place to keep the belt attached for the next steps.


*MOTOR MOUNT (GEARED) | INSTALLING MOTOR MOUNT

2.1 PREP TO INSTALL THE MOTOR MOUNT Take the Gearbox assembly and open the Side_Latch_v2 on the side that shares a hinge with the Hatch. Next, flip open the Hatch.

INSTALL THE MOTOR MOUNT
Mate the slot on the Motor_Mount to the dovetail on the Gearbox. Just get it started, then proceed to the next page.


*MOTOR MOUNT (GEARED)

2.1 INSTALLING THE MOTOR MOUNT
Press down on the Motor_Mount. It should be a snug fit. As you come to the last ~5mm of travel, double-check to make sure that the MR85ZZ bearings are aligned to their slots.

Keep going until the bottom of the Motor_Mount is flush with the bottom of the Gearbox.

INSTALLING MOTOR MOUNT

FINISHING THE MOTOR MOUNT
Close the Hatch and Side_Latch_v2. Install an M3x8mm bolt to hold the Hatch shut. It doesn’t need to be tight - it just holds the MR85ZZ bearings in place.

Then, make sure that the grub screws on the pulley part of the M4_80T_Wheel are fully tightened, with one to the flat of the Drive Shaft.

Next, tension the 188mm GT2 belt loop by lightly twisting the motor counter-clockwise, and give the screws going into the Motor a final tighten. Triple-check that the Drive Shaft spins freely and smoothly.

If the Drive Shaft isn’t running smoothly at any point, undo your most recent assembly step and try again. It is normal for the motor and gear to add some drag.

Finally, install an M3x20mm bolt to hold the Motor_Mount to the Gearbox.

*MOTOR MOUNT (GEARED) | FINISHING THE MOTOR MOUNT

M3x20mm SHCS

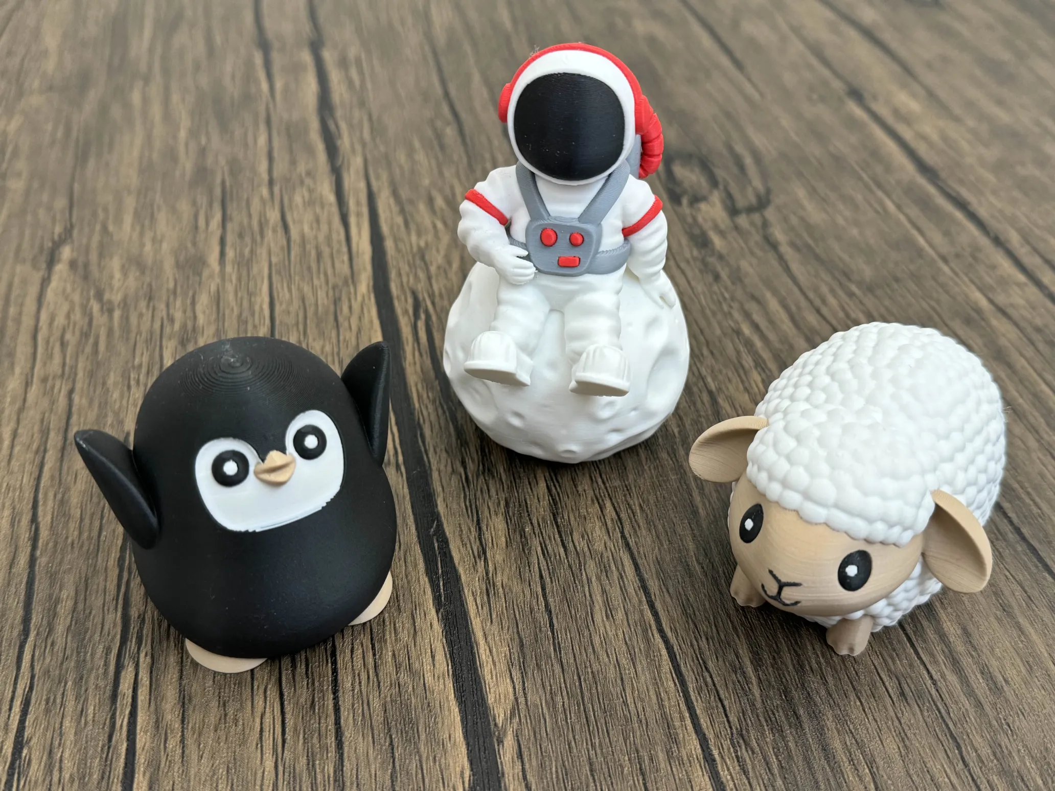
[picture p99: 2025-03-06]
Documentation/assets/example_mmu_print.png

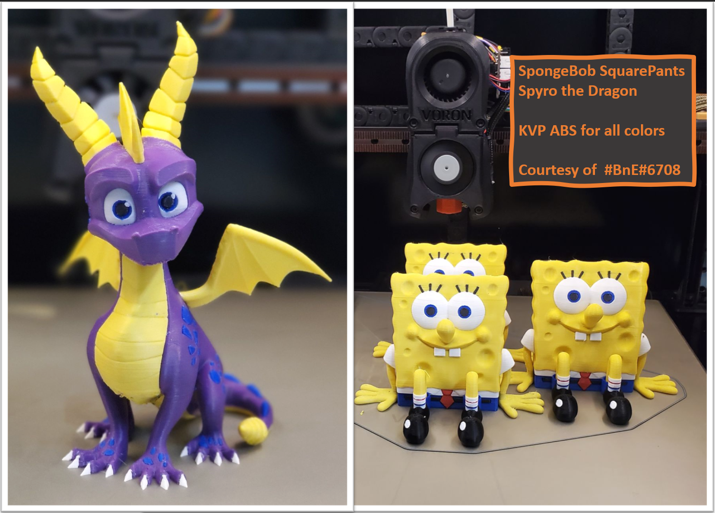
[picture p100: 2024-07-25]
Assets/Showroom/BnE_Prints.png

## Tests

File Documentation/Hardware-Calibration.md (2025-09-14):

## Page Sections:
- [Calibration Steps](#---calibration-steps)
  - [1. Servo](#---step-1-calibrate-your-servo)
  - [2. Selector Offsets](#---step-2-calibrate-selector-offsets)
  - [3. Springy Tension](#---step-3-springy-calibration)
  - [4. Gear Stepper](#---step-4-calibrate-your-gear-stepper)
  - [5. Encoder](#---step-5-calibrate-your-encoder)
  - [6. Bowden Length](#---step-6-calibrate-bowden-length)
  - [7. Gates](#---step-7-calibrating-individual-gates)
- [Calibration Storage](#---calibration-storage)

*\[This guide was adapted from the [Happy Hare Wiki](https://github.com/moggieuk/Happy-Hare/wiki) for ERCF v2.5. Thanks Moggie!\]*

This discussion assumes that you have setup and debugged your [Hardware Configuration](https://github.com/Enraged-Rabbit-Community/ERCFv2/blob/master/Documentation/Hardware-configuration-checks.md).

Before using your ERCF you will need to calibrate it to adjust for differences in components used on your particular build. Be careful to calibrate in the recommended order because some settings build and depend on earlier ones. Happy Hare now has automated calibration for some of the traditionally longer steps and does not require any Klipper restarts so the process is quick and painless.

Upon starting your printer, you should be greeted by a large warning on your console:

```yml
Prerequsite calibration steps are not complete:
Use MMU_CALIBRATE_SELECTOR to calibrate selector for gates: 0,1,2,3,4,5,6,7
Use MMU_CALIBRATE_GEAR (with gate 0 selected) to calibrate gear rotation_distance on gate: 0
Use MMU_CALIBRATE_ENCODER (with gate 0 selected)
Use MMU_CALIBRATE_GEAR (with gate selected) or MMU_CALIBRATE_GATES GATE=xx to calibrate gear rotation_distance on gates: 1,2,3,4,5,6,7
Use MMU_CALIBRATE_BOWDEN
```

Let's take care of that next!

## #f03c15 #c5f015 #1589F0 Calibration Steps

> [!IMPORTANT]  
> When calibrating the first time you must perform calibration in the prescribed order.  Once complete you can re-calibrate particular steps but remember that some calibration changes will cascade.  E.g. after calibrating the gear, you must recalibrate the encoder, the bowden and possibly all the `gear_rotation_distances`.  Generally you can re-calibrate the servo (step 1) selector (step 2) and the gates (step 7) at any time, but the gear, encoder and bowden must always be done in that order!

```mermaid
graph TD;
    Hardware_Working --> MMU_SERVO["2.MMU_SERVO<br/><span style='font-size:10px'>(if fitted)</span>"]
    Hardware_Working --> MMU_CALIBRATE_SELECTOR["1.MMU_CALIBRATE_SELECTOR<br/><span style='font-size:10px'>(if MMU has a selector)</span>"]
    MMU_CALIBRATE_SELECTOR --> MMU_CALIBRATE_BOWDEN
    MMU_SERVO --> MMU_CALIBRATE_GEAR["3.MMU_CALIBRATE_GEAR<br/><span style='font-size:10px'>(can use on every gate to set rotation_distance)</span>"]
    MMU_CALIBRATE_GEAR --> MMU_CALIBRATE_ENCODER["4.MMU_CALIBRATE_ENCODER<br/><span style='font-size:10px'>(if MMU has an encoder)</span>"]
    MMU_CALIBRATE_ENCODER --> MMU_CALIBRATE_BOWDEN["5.MMU_CALIBRATE_BOWDEN<br/><span style='font-size:10px'>(can use to set length on every gate)</span>"]
    MMU_CALIBRATE_BOWDEN --> MMU_CALIBRATE_GATES["6.MMU_CALIBRATE_GATES<br/><span style='font-size:10px'>(available if MMU has an encoder)</span>"]

    style Hardware_Working stroke-width:0px
    style MMU_SERVO stroke-dasharray: 5 5, stroke:#c5f015, stroke-width:2px
    style MMU_CALIBRATE_SELECTOR stroke-dasharray: 5 5, stroke:#c5f015, stroke-width:2px
    style MMU_CALIBRATE_ENCODER stroke-dasharray: 5 5, stroke:#1589f0, stroke-width:2px
    style MMU_CALIBRATE_GATES stroke-dasharray: 5 5, stroke:#1589f0, stroke-width:2px
```
<!--
```mermaid
graph TD;
    LINEAR_SELECTOR["If MMU has Selector"]
    ENCODER["If MMU has Encoder"]

    style LINEAR_SELECTOR stroke-dasharray: 5 5, stroke:#c5f015, stroke-width:2px
    style ENCODER stroke-dasharray: 5 5, stroke:#1589f0, stroke-width:2px
```
-->

- For ERCF, Happy Hare keeps a `rotation_distance` on each gate which requires separate measured calibration of each gate, using `MMU_CALIBRATE_GEAR` or, using the encoder, with `MMU_CALIBRATE_GATES` to automate the process. This is important even if the drive gears are from the same vendor look similar. 

> [!TIP] 
> All of the calibration commands can be run in a "check/test" mode. Simply add `SAVE=0` to the command and the calibration will be run but the results will not be saved. This is very useful to practice or to verify calibration.

### #f03c15 #c5f015 #1589F0 Step 1. Calibrate your servo

Now it's finally time to install the servo arm!

Run the command `MMU_SERVO POS=down`. This will set the servo to the initial down position while you attach the servo arm.

Attach the servo arm, at about 90 degrees, perpendicular to the servo body. *Be careful not to twist the Servo splines while adding the arm - if you do, stop and run the previous command again!* Add the servo arm screw.

Next, tighten down the M3x10mm BHCS that clamps the servo arm down on the servo drive shaft splines. This will make an impression of the splines, locking the servo arm in place.

Happy Hare sets up theoretically good servo postions during installation, however they should be calibrated. ERCF *requires* precise servo calibration to work correctly. To get that precision, you need to run through this process to update and record the correct angle for the `UP` position. Refer to the pictures below to see what each of the servo arm positions should look like.

```yml
MMU_SERVO POS=up
  (Assume the position isn't quite right)
MMU_SERVO
Current servo angle: 125, Positions: {'down': 110, 'up': 125, 'move': 110}
  (Without arguments you can view the current angles)
MMU_SERVO ANGLE=128
  (Tweak until you are happy with the "up" position as compared to the picture below)
MMU_SERVO POS=up SAVE=1
  (Save the current angle (128) for the "up" position)
```

Repeat for the other two positions (`DOWN` and `MOVE`).

> [!NOTE]  
> Servos have a limited range of rotation. If you are unable to attain the servo angle required you might need to reposition the servo arm on the servo, or edit the servo configuration in `mmu_hardware.cfg`
 
**Servo positions on ERCF**

Make sure the `MOVE` and `UP` positions of your servo arm are set so that the arm does not hit the tophats when the selector is moving. See picture below to see where the servo arm should be for the 3 positions.

- Servo Up. This position releases the filament trap for printing without sync mode.

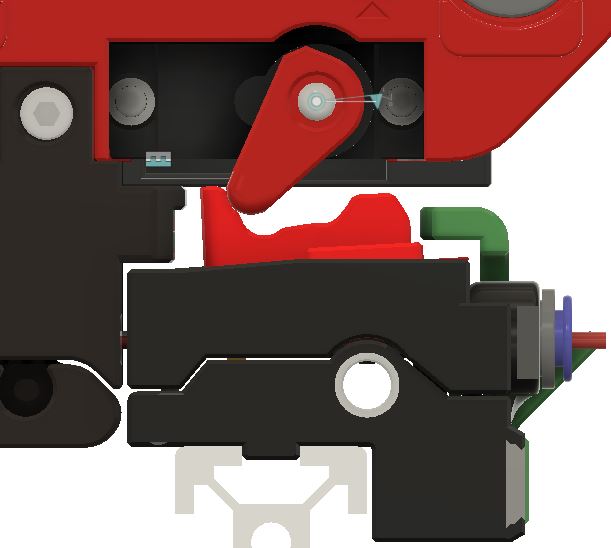
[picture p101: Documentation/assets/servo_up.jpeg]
Servo Up


- Servo Move. This position activates the filament trap so that the Selector can move.

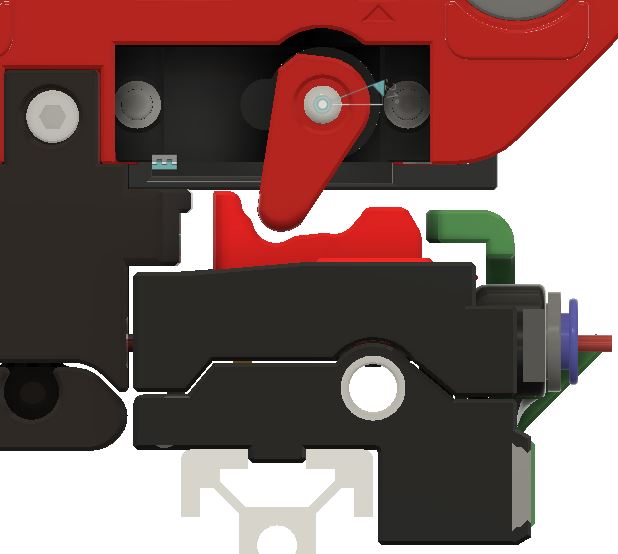
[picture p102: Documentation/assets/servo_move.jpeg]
Servo Move


- Servo Down. This position meshes the BMG gears to push filament. The filament trap is released to allow for Load/unload or to print with sync mode)

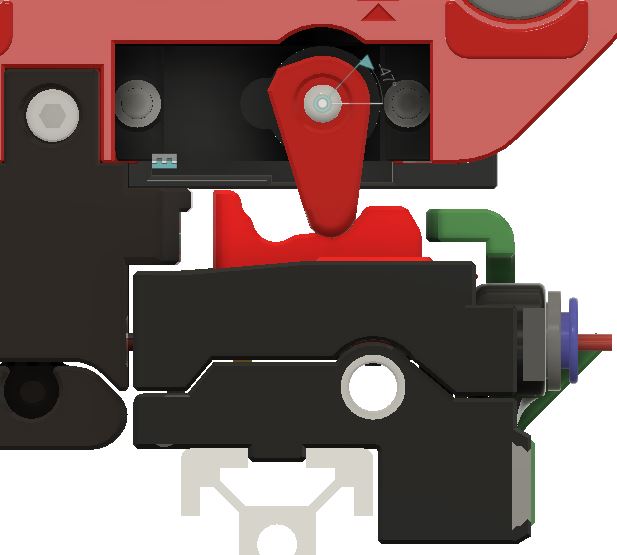
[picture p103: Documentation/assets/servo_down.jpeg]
Servo Down


**If the servo angles are set incorrectly, the servo will struggle to reach the angle set, which will reduce the servo's lifetime, and may even burn the servo out! You will know if the servo is struggling to reach position because it will keep buzzing while it tries to reach the set angle.**

> [!NOTE] 
> It is normal for the Gear motor to move back and forth slightly during a `MMU_SERVO POS=down` command. This is to ensure that the BMG gears mesh properly.

Once you are satisfied with your angles, you are done with this step!

### #f03c15 #c5f015 #1589F0 Step 2. Calibrate selector offsets

First, make sure that there is room between the endstop and Gate 0. We don't want the endstop to be activated while using Gate 0, instead we want there to be at least a 1.0mm gap between the two positions. If the endstop is activated when using Gate 0, you need to tighten the endstop adjustment screw (the BHCS on the Encoder). If for the endstop isn't activating even at the end of travel, the endstop adjustment screw needs to be loosened. The screw has a pitch of 0.5mm, so one full turn will move it in or out 0.5mm.

Once you have the endstop distance adjusted, There are three ways to calibrate the selector offsets:

#### A) Fully automatic calibration
Let's start by getting the selector cailbrated in this easy step (it is important to do this early because the bowden and gate calibration need to be able to select gates). This sets up the position all of all the gates as well as the bypass position if fitted. Firstly ensure MMU motors are off by running `MMU_MOTORS_OFF` and remove filament from gate #0 -- you may need to run `MMU_SERVO POS=up` to release the filament. Then re-insert and remove filament through selector to ensure that gate #0 is correctly alined with selector. Be careful and move the selector side to side whilst moving the filament inside the gate. Try to assess where the filament is centered in the gate and leave the selector in that position. Then run:

  > MMU_CALIBRATE_SELECTOR

Sit back and relax. The selector will move to find the extremes of movement and then use information about the geometry of the particular MMU and version/options you are using to generate and save the selector offsets automatically!

#### B) Extrapolate first and last gates
Although the automated method above will attempt to calibrate the Selector, it can result in drift unless all the gates/lanes are perfectly tight together. To address this a better method that can be used with ERCF v2.5 is as follows:
```yml
MMU_MOTORS_OFF
  (Use a piece of filament to align gate 0; remove filament)
MMU_CALIBRATE_SELECTOR GATE=0
MMU_MOTORS_OFF
  (Use a piece of filament to align the last gate; remove filament)
MMU_CALIBRATE_SELECTOR GATE=n
  (where n is the last gate number, remember we are 0 based)
```
This will automatically set the offset of all intermediate gates distributing any build variance

#### C) Individual gate calibration
Although it should not be necessary other than for the bypass gate, there is an option update a single position if you would like to tune or run into problems. See the command reference for more detailed information on options, but basically, you turn MMU motors off, line up the desired gate with the selector and run:

  > MMU_CALIBRATE_SELECTOR SINGLE=1 GATE=...

Strictly speaking `SINGLE=1` is only required if calibrating just your final gate to avoid automatic extrapolation.

#### C part 2) Bypass gate calibration
ERCF has a built-in bypass gate. Similar to the above step, you can calibrate it's position by aligning the selector and running:

  > MMU_CALIBRATE_SELECTOR BYPASS=1

**Validation:** At the end of this step you should be able to select any tool/gate on your MMU. For instance, try running `MMU_HOME TOOL=3` to re-home and select tool/gate #3.

### #f03c15 #c5f015 #1589F0 Step 3. Springy Calibration

*You should start with the Springy adjustment bolt only just touching the Spring Cap part, with little to no tension on the spring.*

Put a scrap of PTFE into Gate 0. Run the command `MMU_SELECT GATE=0`.

Feed a **new** piece of filament at least 250mm long into Gate 0 and past the encoder.

Run the command `MMU_TEST_GRIP`

Pull on the filament in the unloading direction. The gears should grip the filament and move the entire Drive Shaft as you pull. 

If the filament slips on the gears at all, tighten the Springy tensioner bolt, half a turn at a time, until the filament is fully and firmly gripped by the drive gears when you pull. Run this test on every channel.

If the grip is too strong, eg. the filament is being mangled by the gears, or the filament is grinding, tighten the anti-squish screw by a quarter turn and test again.

It is important to set the Springy tension and antisquish screws correctly so that the drive gears have good grip on the filament. If this is not set correctly, later calibration steps may give erroneous readings, because the length of filament sent by the Gear Motor is used in the calibration calculations.

The Springy spring tensions the Servo downward, while still allowing the Servo to flex upwards slightly as necessary during operation. The antisquish screw prevents the tension from squishing the filament too much.

### #f03c15 #c5f015 #1589F0 Step 4. Calibrate your gear stepper
**It is Very Important to get this right!**

In this step you are ensuring that when the gear stepper is told to move 100mm of filament it really does move 100mm.  It is akin to what you did when you set up your extruder rotational distance, although in this case no Klipper restart is necessary!  Select gate #0 (you can use `MMU_SELECT GATE=0` if you have finished the selector calibration above) and put some filament through the gate so that it pokes out just past the selector exit.  Run the following to ensure the filament is gripped if your MMU needs to actuate a servo to grip filament:

  > MMU_SERVO POS=down

Next remove the bowden tube and cut the filament flush with the ECAS connector at the output of the MMU (e.g the encoder on the ERCF design). Run this command to attemp to move 100mm of filament:

  > MMU_TEST_MOVE MOVE=100

Get out your ruler and very carefully measure the length of the emited filament.  Hold your ruler up to the bowden and gently pull the filament straight to get an accurate measurement. Next run this specifying your actual measured value (102.5 used in this example):

  > MMU_CALIBRATE_GEAR MEASURED=102.5

```
    Gear stepper 'rotation_distance' calculated to be 23.117387 (currently: 22.9)
    Gear calibration for gate 0 has been saved
```

> [!TIP]  
> You can also measure over a different length by using something like `MMU_TEST_MOVE MOVE=200` and `MMU_CALIBRATE_GEAR LENGTH=200 MEASURED=205.25` for a 200mm length for example. Don't forget the `LENGTH=200` argument, or it the calibration calculation will default to 100mm and set your gear calibration wrong!

> [!IMPORTANT]
> The value for `rotation_distance` should be between 22 and 24 for BMG gears - if you get a `rotation_distance` far outside of these values, something has likely gone wrong! Redo this step. Common mechanical causes include overtensioned Selector belts and misaligned Selector positions.

**Validation:** If you want to test, snip the filament flush with the ECAS connector again and run `MMU_TEST_MOVE`.  Exactly 100mm should be moved this time.

You can either repeat this for all other gates, or you can shortcut and use `MMU_CALIBRATE_GATES` in Step 7.

### #f03c15 #c5f015 #1589F0 Step 5. Calibrate your encoder

The next step is to calibrate the Encoder so it measures distance accurately. Re-fit the bowden to the encoder output. Alternatively, just make sure you have at least 500mm of filament at gate #0 before starting. Now run:

  > MMU_CALIBRATE_ENCODER

You will see an output similar to:

```
    Calibrating over 400mm...
      + counts: 368
      - counts: 368
      + counts: 369
      - counts: 369
      + counts: 369
      - counts: 369
    Load direction:   mean=368.67 stdev=0.58 min=368 max=369 range=1
    Unload direction: mean=368.67 stdev=0.58 min=368 max=369 range=1
    Before calibration measured length: 394.47mm
    Calculated resolution of the encoder: 1.085049 (currently: 1.094543)
    Encoder calibration has been saved
```

> [!NOTE]  
> (i) Use fresh filament - grooves from previous passes through extruder gears can lead to slight count differences.
> (ii) Make sure the selector is aligned with the gate. If it is off to one side you will almost certainly get dissimilar counts in forward and reverse directions.
> (iii) You want the counts on each attempt to be the same or very similar but don't sweat +/-3 counts.  Between the spring-tensioned servo and Binky encoder design they should be very consistent ;-)
> (iv) You can run this (like all calibration commands) without saving the result by adding a `SAVE=0` flag.

If this step worked then you should be able to unload the residual filament with `MMU_UNLOAD`. If you aren't happy with results, leave the filament ready for the next run and repeat this section.

### #f03c15 #c5f015 #1589F0 Step 6. Calibrate bowden length

Here you can calibrate the length of your bowden from MMU gate to extruder entrance. This is important because it allows the MMU to move the filament at a fast pace over this distance before getting to the more complicated part of the load sequence. To speed up this process, and depending on what sensors you have fitted for extruder homing, you may need to give the calibration routine a hint of how far way the extruder is.

There are different ways to do this depending on your configuration and sensor options:

1. If `extruder_homing_endstop: extruder` (or `mmu_gear_touch` or `filament_compression`), then you have a homing endstop and you can simply specify a `BOWDEN_LENGTH` that is GREATER than your estimated length to give plenty of room to find the homing stop.

  > MMU_CALIBRATE_BOWDEN BOWDEN_LENGTH=1500

2. If you are using `extruder_homing_endstop: collision`, then the `BOWDEN_LENGTH` supplied MUST be slightly shorter than the actual length. A good rule of thumb is to manually measure the distance from exit from the selector to the entrance to your extruder. Subtract 40-50mm from that distance. I measured approximately 690mm on my system, so will supply 650mm as the starting value. For example:

  > MMU_CALIBRATE_BOWDEN BOWDEN_LENGTH=650

```
    Homing MMU...
    Tool T0 enabled
    Calibrating bowden length from reference Gate #0
    Tool T0 enabled
    Heating extruder to minimum temp (200.0)
    Finding extruder gear position (try #1 of 3)...
    Pass #1: Filament homed to extruder, encoder measured 683.5mm, filament sprung back 3.2mm
    - Bowden calibration based on this pass is 683.5
    Finding extruder gear position (try #2 of 3)...
    Pass #2: Filament homed to extruder, encoder measured 682.7mm, filament sprung back 3.2mm
    - Bowden calibration based on this pass is 682.7
    Finding extruder gear position (try #3 of 3)...
    Pass #3: Filament homed to extruder, encoder measured 683.9mm, filament sprung back 3.2mm
    - Bowden calibration based on this pass is 683.4
    Recommended calibration reference is 680.2mm. Clog detection length: 16.8mm
    Bowden calibration and clog detection length have been saved
```

3. Finally, if you run into problems with collision detection at the extruder, you can run manual calibration. To do this, select gate 0, push filament through manually all the way to the extruder gears. This run `MMU_CALIBRATE_BOWDEN MANUAL=1` option. This will measure the distance in reverse to the gate homing position:

  > MMU_CALIBRATE_BOWDEN BOWDEN_LENGTH=1000 MANUAL=1

This will reverse home to the gate and uses Klipper's measurement of stepper movement.

> [!NOTE]  
> (i) This calibration assumes that the selector has been calibrated first.
> (ii) This may cause the extruder to be heated. This is to ensure that the extruder motor is energized and can resist the impact of the collision with the filament

### #f03c15 #c5f015 #1589F0 Step 7. Calibrating individual gates

This step allows for calibrating slight differences between gates and saves you from having to use `MMU_CALIBRATE_GEAR` on every gate. Even with ERCF this is optional because if not run, the gates will tune themselves as they are used automatically!  That said it be beneficial to get this out of the way with a test piece of filament, but doing it also: (i) removes the need to set the `autotune_rotation_distance` in `mmu_parameters.cfg`, (ii) is necessary if there is substantial variation between gates -- e.g. if BMG gears for different gates are sourced from different vendors.

Simply make sure filament is available at the gate you want to calibrate (you can also insert a 500mm piece of filament) and run:

> MMU_CALIBRATE_GATES GATE=1

You will see an output similar to:

```
    Tool T1 enabled
    Calibrating gate 1 over 400.0mm...
      + measured: 404.4mm
      - measured: 404.4mm
      + measured: 404.4mm
      - measured: 404.4mm
      + measured: 405.5mm
      - measured: 405.5mm
    Load direction:   mean=404.7 stdev=0.63 min=404.4 max=405.5 range=1.1
    Unload direction: mean=404.7 stdev=0.63 min=404.4 max=405.5 range=1.1
    Calibration move of 6x 400.0mm, average encoder measurement: 404.7mm - Ratio is 1.011872
    Calculated gate 1 rotation_distance: 22.941324 (currently: 22.672165)
    Calibration for gate 1 has been saved
```

> [!NOTE]  
> (i) You can also quickly run through all gates (and even pass the loose filament gate to gate) with `MMU_CALIBRATE_GATES ALL=1` <br>
> (ii) If you see "Calibration ignored because it is not considered valid (>20% difference from gate 0)" then it either means the calibration failed because filament was not moving correctly, or the encoder was not working correctly. Less likely but possible is because you have not calibrated gate 0 (`MMU_CALIBRATE_GEAR` and `MMU_CALIBRATE_ENCODER`) correctly which serves as the reference gate.

> [!IMPORTANT]
> The value for `rotation_distance` should be very close to the `rotation_distance` from step 4 - if you get a `rotation_distance` that is very different, something has likely gone wrong! Redo this step. Common mechanical causes include overtensioned Selector belts and misaligned Selector positions.

### #f03c15 #c5f015 #1589F0 Calibration Storage
All calibrated results are stored in the configured `[save_variables]` file. By default and most usually this will be `mmu_vars.cfg`. Here is a list of those variables and the command that sets them:

  | Variable | Command | Notes |
  | -------- | ------- | ----- |
  | mmu_servo_angles | MMU_SERVO | E.g {'down': 45, 'up': 125, 'move': 110} represents the angles for the three servo positions |
  | mmu_gear_rotation_distances | MMU_CALIBRATE_GEAR or MMU_CALIBRATE_GATES | The list represents `rotation_distance` for each gate |
  | mmu_encoder_resolution | MMU_CALIBRATE_ENCODER | The distance each encoder signal transition represents |
  | mmu_selector_offsets | MMU_CALIBRATE_SLECTOR | A list of offsets for each gate of the MMU |
  | mmu_selector_bypass | MMU_CALIBRATE_SELECTOR | The offset of the bypass (passthough) location |
  | mmu_calibration_bowden_home | MMU_CALIBRATE_BOWDEN | Records the gate homing endstop used as a basis for the calibration |
  | mmu_calibration_bowden_lengths | MMU_CALIBRATE_BOWDEN | The list will be the same length as the number of gates on your MMU |
  | mmu_calibration_clog_length | MMU_CALIBRATE_BOWDEN | Only used with encoder although always set incase you add in the future |

Happy Hare documentation lists all [Calibration Commands](https://github.com/moggieuk/Happy-Hare/wiki/Command-Reference#---calibration)
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

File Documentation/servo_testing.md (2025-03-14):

**The following is an unedited log of the testing that Marc performed on various servos over the course of a few months. All I've done is copy every post he made about servos, along with the the images he posted. I also added some of the questions we asked him during testing, for context.**

i whipped up a test setup and tortured a random MG90 today, will repeat the test with savox, guo hua and metal gear mg90 tomorrow evening

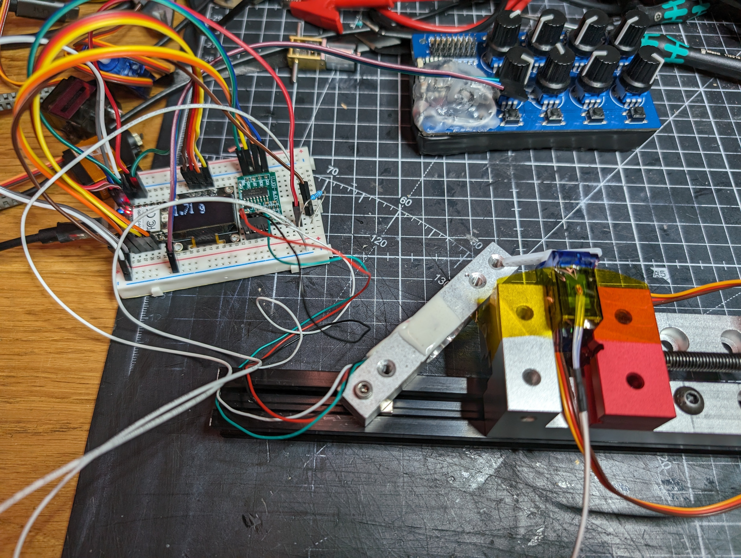
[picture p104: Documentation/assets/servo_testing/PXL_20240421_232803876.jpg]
Servo Test Rig


after ~45 "hard push" actions in short succession (100ms delay between each try) the MG90 is basically about to fail and already started to degrade push performance after 25 pushes

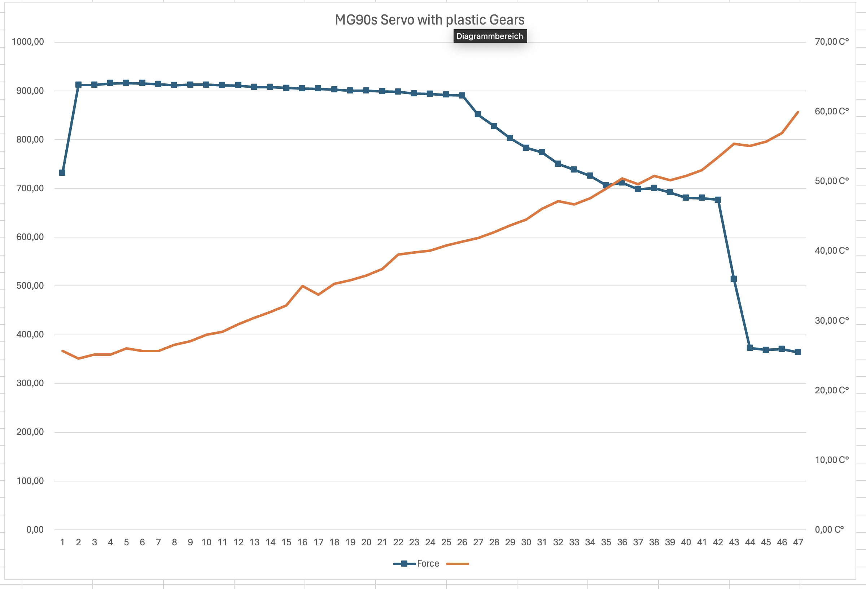
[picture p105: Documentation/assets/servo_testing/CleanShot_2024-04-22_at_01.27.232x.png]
MG90s Servo with Plastic Gears Results


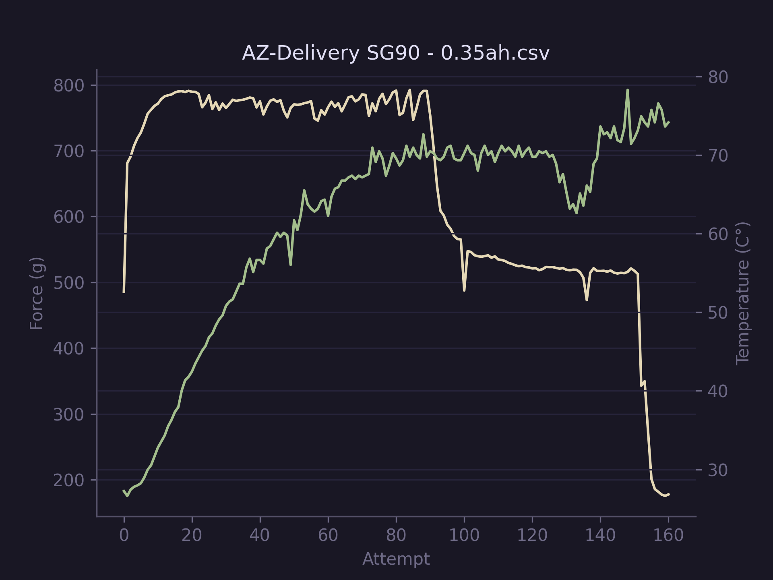
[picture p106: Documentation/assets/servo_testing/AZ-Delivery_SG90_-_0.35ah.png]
AZ-Delivery MG90 Results

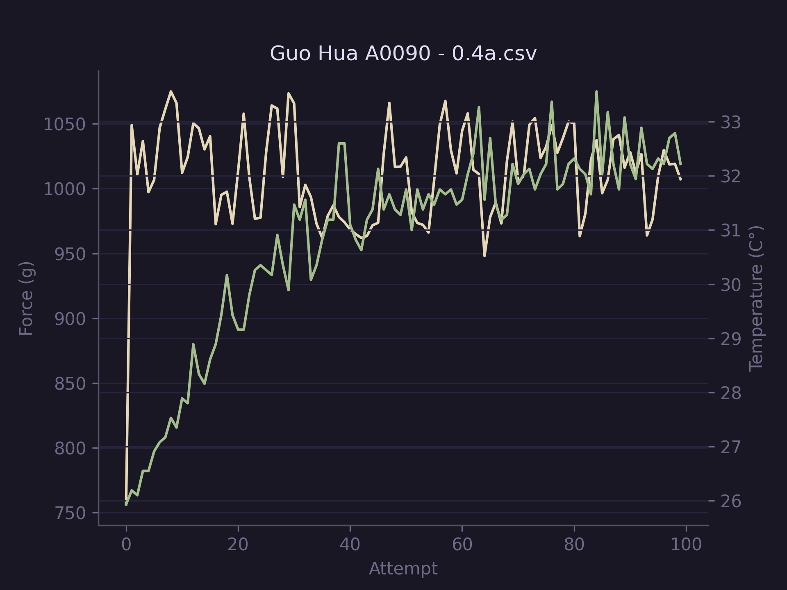
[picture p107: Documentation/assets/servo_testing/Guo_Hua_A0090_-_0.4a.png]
Guo Hua A0090 Results

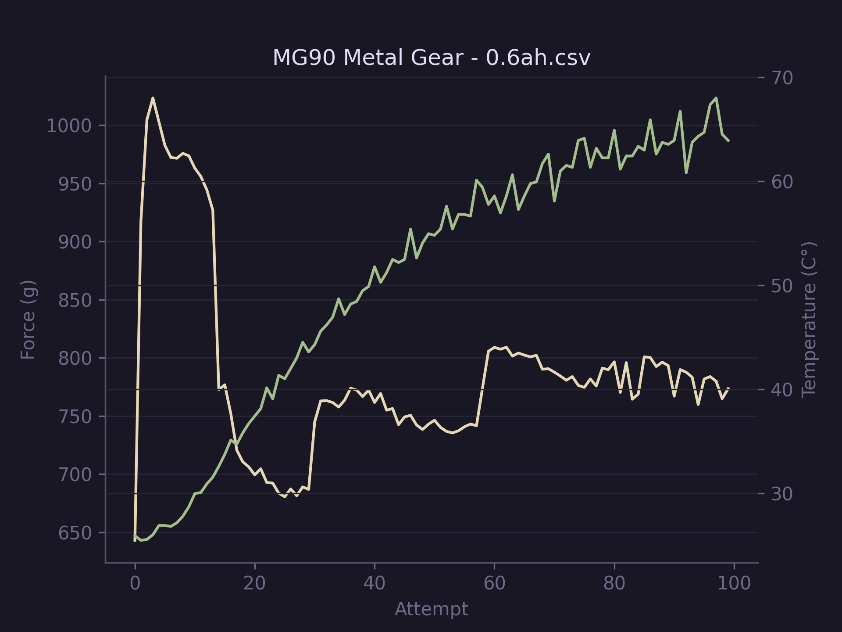
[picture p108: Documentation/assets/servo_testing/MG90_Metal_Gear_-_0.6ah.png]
MG90 Metal Gear Results

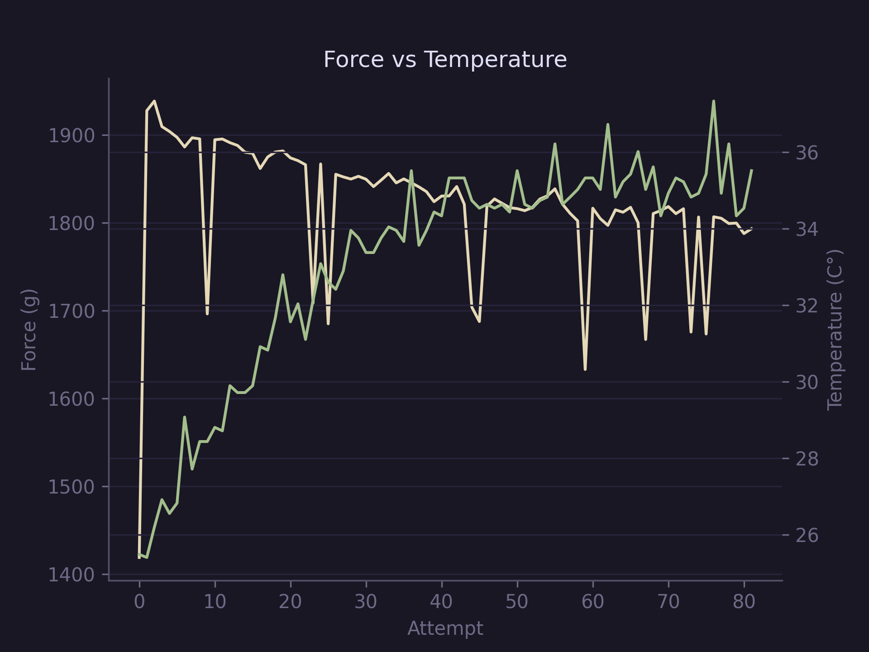
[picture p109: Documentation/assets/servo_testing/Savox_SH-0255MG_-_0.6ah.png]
Savox Force vs Temperature


and here's a comparison, solid lines are the force and dashed the temperature lines, same color same servo

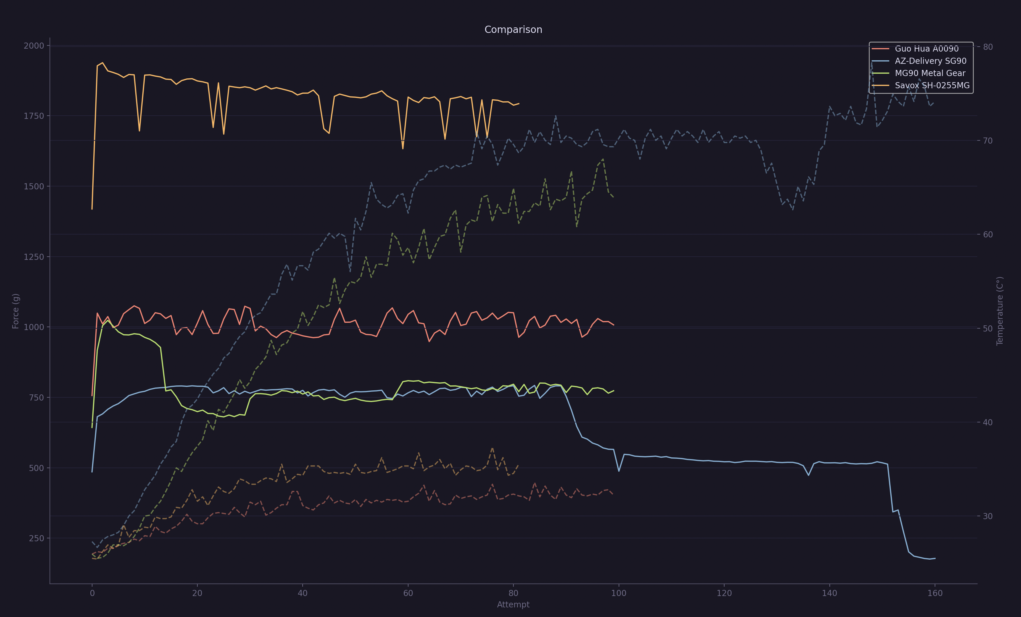
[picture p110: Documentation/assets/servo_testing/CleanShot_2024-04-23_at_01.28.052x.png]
Comparison


so, the Savox beats all others easily, the plastic gear one is really unreliable, the metal gear MG90 is kinda ok and holing on, the Guo Hua seems also pretty solid and stable, but far away form the push power of the savox.
all force and temperature values should be considered rough estimates, because i simply threw together a load cell and ntc temperature probe, but for comparing this is still valid data to see the difference
also, the Savox and Guo Hua stay quite cool, both MG90 variants get hot quick and can lead to permant failure easily when stressed a lot

Guo hua a0090 would be also an option, seems stable and reliable, but not ad strong as the mg90s

here's the gist of the Data i gather so far:

Results Data Table

the SG90/MG90 basically disqualify due to quick heat buildup, A0090 and SH-0225MG keep pretty cool, A0090 does have more push power than the MG90/SG90 but is far behing the SH-0255MG

i just ordered these for Servos for additional tests, give me a shout, if you know of any more i should/could include in these tests, i also ordered an original TowerPro MG90S, since i only got a random clone tested so far

GDW DS041MG (https://gdwservo.com/product/gdw-ds041mg-5kg-torque-metal-gear-micro-mini-digital-servo-for-450-helicopter-fix-wing-rc-auto-robot-arm/)

DSPower DS-S006M (https://www.dspowerservo.com/ds-s006m-metal-gear-9g-servo-micro-servo-product/)

JX Servo PDI-1109MG (http://www.jx-servo.com/en/Product/micro/MD/566.html)

Original TowerPro MG90S (https://www.towerpro.com.tw/product/mg90s-3/)

Servo Tuesday 1
Servo Tuesday 2

Seems to be a Servo Tuesday 

Will start testing tonight

TowerPro MG90S being stressed on the bench, maxes out at 740g so far and already quickly rose to 51.2°C, so far not looking better than the clones, will run through 3000 cycles with 1s pause in between 

well, already started to degrade when it rose to 55°C, so i canceled that run and put on the GDW DS041MG instead, lets see how it'll hold up, change to 5s instead of 1s pause in betrween cycles

GDW DS041MG (~7.5€ on AliExpress) put up a solid performance over night, stable ~800g of push force, quickly rose to ~30°C but didn't rise above 35°C which should be quite fine, this was 3000 attempts at 5s pause 

GDW DS041MG Results

some nerdy stuff, i completely redid the electronics for the test rig and switched form rp2040 to an esp32, so instead of logging to a serial console the data now flows directly into my influxDB which i have running on my HomeAssistant Server anyway. Usually that's a time based logging, but i programmed the esp32 so that the test run always starts at start of epoch and goes from there, so the data is comparable to each other over real timeframes

using that data i can use Grafana to dig in and plot it into graphs, and even publish snapshots to share online: https://snapshots.raintank.io/dashboard/snapshot/K923gpDqSMlkNJxxM6egWdj5cI3GKi1t

so, now i've got the JX PDI-1109MG on the Test bench, temperature looks good so far, similar to the GDW around 30-35°C, but push force seems to be almost 100g less than the GDW at mean:

JX PDI-1109MG (~6€ on AliExpress) kept going stable at the force and temperature over all 3000 attempts, so not as strong as GDW, but it seems to be stable for longer use 

JX PDI-1109MG Results

comparison in one graph of those 2

GDW DS041MG and JX PDI-1109MG Results

next up: CSPower 12G Digital Servo (~4€ on AliExpress)

CSPower 12G Digital Servo (~4€ on AliExpress) is off to a good start:

CSPower 12G Beginning

Servo Size Comparison

second from the right, right next to the original mg90s, a tiny bit smaller

CSPower 12G

i'll do another run with the original towerpro mg90 after this run, but at 1s pause it quickly heated up as well

will give it another chance at 5s like the others right now

yes, Guo Hua and Savöx standing above

will redo both on the latest rig and test firmware as well to have a fair comparison with 3000 tries 5s pause

takes about 5h for one test run 😅

which is also kind of a fair "test" for real world usage imho

i'm running these in a ~20°C room right now sandwiched between 2 aluminium blocks (vise), that should already enable some heat dissapation, now how would they handle in hotter climate?

especially in such cases MG90 might go bad quicker

ProModeler was difficult to source, right?

US only?

44$ and no shipping option to me, so, yea no thanks 😄

CSPower 12G is happily chopping on without signs of degradation:

CSPower 12G preliminary results

so, yea very solid performance for the price for the CSPower 12G Servo:

CSPower 12G results comparison

next i'm rerunning the Savöx as a comparison, already feels like they're playing in different leaques...

Savöx basically "shifts" that whole graph into a new perspective:

Savox results comparison

savöx is the green dot top left

1.53kg average currently

i mean, what really sets the savöx above from the others, is, that it basically doubles the push force of the others while also being the coolest to operate, really suprising considering how similar the others perform: 

would be curious to add ProModeler to the list, though i don't think it'll end up as the recommodation for most people, it'll be difficult to beat Guo Hua performance/price wise and the CSPower seems to be very good for that low price

Guo Hua is available for 6-7€ currently on AliExpress

ea, i'll slap on the guo hua again tomorrow morning, savöx will run for another ~4h

I'd currently group the servos into: 

discouraged: MG90 (Clones and Original)

budget options: CSPower, GDW, JX

default recommodation: Guo Hua

high peformance: Savöx (, maybe ProModeler)

so, Savöx performed very stable, 1560g push force mean and did't exceed 20.5°C, pretty impressive.

Guo Hua is running since this morning, kinda expected a bit more push force, but 776g is still a solid performance so far, pretty happy about the temperature, it's even below the savöx

Guo Hua Results Comparsion

actually you're right the temp of guo huo does not make sense, need to investigate, because this is the temp in the room for the last 24h:

Room Temp

i'd put out basically this: 

discouraged: MG90 (Clones and Original) [tests have shown degrading push power and thermal problems in stress tests]

budget options: CSPower 12g, GDW DS041MG, JX PDI-1109MG

default recommodation: Guo Hua A0090

high peformance: Savöx 0255MG (, maybe ProModeler)

will do, i'll investigate the guo huo temperature later tonight and add a final run of the original tower pro which is missing right now, then i'll announce that in the vendor chat with some data, prices, etc.

to be honest, i'm a bit confused right now, doing another test with another random XTVTX MG90 looks like this so far:

XTVTX MG90 preliminary results
XTVTX MG90 results comparison

will do at least one other XTVTX to compare

i am collecting voltage and current, but the sensors i have seem to be shit, so not really usable data

i can read about 0.254A on my lab power supply on this run currently

additionally connected to usb though, so probably not the full picture

the other XTVTX MG90 i tested did degrade after 1000-2000 tries:

XTVTX MG90 degradation

Maybe the other one was bad

Will try ~100 attempts with every clone i have to get a "range"

well, just came back from outside...

good impression didn't last:

XTVTX MG90 failure

VIDEO

Houston, we've got a failed MG90S clone

Yes, it was probably still "fresh" but went bad quick

Broken plastic gears

1 gear failed completely and one lost one tooth

should i try to destroy another? 😄

i put on the original TowerPro MG90s instead, let's see if it also shares that same fate

well, i'd say there's already kind of a trend visible:

TowerPro MG90S Trend Beginning

These are the original TowerPro MG90s.

`What good are these motors if they fail so badly. Must be for the very lightest toys.`

yea, especially because these 2 variants are basically the "only" servos you get when searching amazon for small servos:

can't get Guo Hua A0090, GDW DS041MG, JX PDI-1109MG or CSPower 12g on amazon here in germany

i need to source all of them from ali

trend does seem to continue:

TowerPro MG90S Trend continuing

seems to stabilize so far:

TowerPro MG90S stablized

i had to restart that test, the servo arm startet slipping/stripping out on that test (bottom graph), the new test was stable over 3000 attempts:

TowerPro MG90S stable?

so, overall the TowerPro Original did similar to the other good servos:

TowerPro MG90S Comparison

will slap a final clone on the bench to see if it also fails

still doing more tests on the MG90 clones, 2 did quite ok so far, one failed with brokes gears and the on on it right now quickly dipped in performance but is stable so far, but it does make a struggling sound, so might fail during this test :

XTVTX MG90 prolonged testing

short status quo, still testing, so far 5 XTVTX Servos, suprisingly most are putting up a good performance aside from the one that failed with broken gears and one (Number 4) which did not work at all, so it's missing in the graph:

XTVTX MG90 mixed bag

there is quite a bit variation in push force though

`The manufactured consistency sounds like a big issue to me despite the performance`

yea, currently i'd still recommend one of the others, kinda expected number 3 to fail as well, it was very noisy, almost crying to be released from it's misery, while pushing

`yeah in my opinion 2 out of 5 being defective is horrible even before performance testing. In my opinion if it is any worse than 1% of 100 samples, that's hugely iffy.`

I'll do additional tests with the others as well to see how they stack up

`have you tested the GDW DS041MG as of yet?`

yes, worked pretty good:

GDW DS041MG results

the #7 of XTVTX MG90 did some funky stuff at the, will do another round for that one:

XTVTX MG90 #7 mixed bag

so, yea this #7 of the XTVTX MG90s really does some wonky stuff, (blue round 1, red round 2)

XTVTX MG90 #7 mixed bag

BTW, i've collected almost 50 000 force measurments by now 

`There are more GDW issues showing up on Facebook now too.`

i'll put on one of the other GDW after this MG90 testrun in ~1h

i got 4 GDX here i can test

#7 is really a weird one, expected it to completely fail, but seems like it'll go out with decent values, still the weird spikes  and variance of performance would disqualify it for me

XTVTX MG90 mixed bag

started testrun on GDW #2

GDW DS041MG #2 results

second GDW performt quite consistend, i think i've got the lever arm a bit further out which explains the differnt push force

#3 GDW is also performing similar to the #2 so far

`bad batch then, or is it bad software configuration I wonder?`

this only tests force + temperature currently

not speed

i'm waiting 100ms after initializing the move to measure

so, let's print a "batch" test jig 😅
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

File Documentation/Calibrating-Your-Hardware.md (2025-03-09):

#### Page Sections:
-MMBv1.1:
  - [Flashing Katapult onto MMBv1.1](#---flashing-katapult-for-mmbv11)
  - [Compiling Klipper for MMBv1.1](#---compiling-klipper-firmware-for-mmbv11)

## #f03c15 #c5f015 #1589F0 Calibrating Your Hardware

To Be Written (Soon!)

Basically, you need to calibrate your servo and Springy and run some calibrations, and this page will show you how.

-Hardware confirmations that everything is 1. moving and 2. in the right direction
-Selector Endstop screw adjustment (kind of software? Needs to leave space between home position and Gate 0)
-Servo arm installation and setting servo angles (which is kind of software too?)
-Springy tension calibration

## Step 1. Check Endstop & Optional Sensors

Verify that the Selector endstop, and any installed extruder or toolhead sensors are working. The recommended procedure is:

`MMU_MOTORS_OFF`

Now remove filament from ERCF and extruder, and move the Selector to the center of travel.

`QUERY_ENDSTOPS`

(Or use the visual query in Mainsail or Fluuid). Validate that you can see:

```yml
mmu_sel_home:open
extruder:open
toolhead:open
[...]
```

> [NOTE]
> You will only see the sensors you have installed. You will additionally see any endstops or sensors installed on your printer.

Then manually press and hold the selector microswitch and rerun `QUERY_ENDSTOPS`.

Validate that you can see `mmu_sel_home:TRIGGERED` in the list.

If you have an extruder sensor installed, feed filament into the extruder past the switch and rerun `QUERY_ENDSTOPS`.

Validate that you can see `extruder:TRIGGERED` in the list.

If you have a toolhead sensor installed, feed filament into the toolhead past the switch and rerun `QUERY_ENDSTOPS`.

Validate that you can see `toolhead:TRIGGERED` in the list.

If any of these don't change state, then the pin assigned to the endstop is incorrect. If the state is inverted (i.e. enstop transitions to `open` when pressed) then add/remove the `!` on the respective endstop pin in `mmu_hardware.cfg`. 

Other endstops like "touch" operation and pregate sensors are advanced and are not cover by this inital setup.

## Step 2. Check motor movement and direction

Once pins are correct it is important to verify direction.  It is not possible for the installer to ensure this because it depends on the actual stepper wiring.  The recommended procedure is:

Run the command `MMU_MOTORS_OFF` Now move the Selector to the center of travel. 

Next, run the command `MMU_HOME` and verify that the Selector moves towards the endstop / home position

If the Selector doesn't move it is likley that the pin configuration for `step_pin` and/or `enable_pin` are incorrect. Open up `mmu_hardware.cfg`, and find the section `[stepper_mmu_selector]`.

Verify the pin names and prefix the pin with `!` to invert the signal. E.g.

```yml
enable_pin: !mmu:MMU_SEL_ENABLE
 (or)
enable_pin: mmu:MMU_SEL_ENABLE
```

If the selector moves the wrong way the `dir_pin` is inverted. Either add or remove the `!` prefix:

```yml
dir_pin: !mmu:MMU_SEL_DIR
 (or)
dir_pin: mmu:MMU_SEL_DIR
```

Now repeat the exercise with the gear stepper:

```yml
MMU_MOTORS_OFF
  (remove any filament from your MMU)
MMU_TEST_MOVE MOVE=100 SPEED=50
  (verify that the gear stepper would pull filament towards the extruder)
MMU_TEST_MOVE MOVE=-100 SPEED=50
  (verify that the gear stepper is pushing filament away from the extruder)
```

If the gear stepper doesn't move or moves the wrong way open up `mmu_hardware.cfg`, find the section `[stepper_mmu_gear]`:<br>
If gear doesn't move it is likley that the pin configuration for `step_pin` and/or `enable_pin` are incorrect. Verify the pin names and prefix the pin with `!` to invert the signal. E.g.

```yml
enable_pin: !mmu:MMU_GEAR_ENABLE
 (or)
enable_pin: mmu:MMU_GEAR_ENABLE
```

If the gear moves the wrong way the `dir_pin` is inverted. Either add or remove the `!` prefix:

```yml
dir_pin: !mmu:MMU_GEAR_DIR
  # or
dir_pin: mmu:MMU_GEAR_DIR
```

## Step 3. Check the Encoder

We need to check that the Encoder is wired correctly. Run the command `MMU_ENCODER` and note the position displayed.

```yml
MMU_ENCODER
Encoder position: 23.4
```

Insert some filament (from either side) and pull backwards and forwards.  You should see the red LED flashing behind the enraged rabbit's eyes. Rerun `MMU_ENCODER` and validate the position displayed has increased (note that the encoder is not direction aware, so it will always increase in reading).

If the encoder postion does not change, validate the `encoder_pin` is correct. It shouldn't matter if it has a `!` (inverted) or not, but it might require a `^` (pull up resister) to function.

```yml
[mmu_encoder mmu_encoder]
encoder_pin: ^mmu:MMU_ENCODER	
```

## Step 5. Check other sensors (if fitted)

Other sensors are generally filament sensors and act on a switch. The easiest way to check these is to run something similar to the following for each sensor/switch.

```yml
QUERY_FILAMENT_SENSOR SENSOR=mmu_gate_sensor
Filament Sensor mmu_gate_sensor: filament not detected
```

Activate the sensor with a piece of filament and run again:

```yml
QUERY_FILAMENT_SENSOR SENSOR=mmu_gate_sensor
Filament Sensor mmu_gate_sensor: filament detected
```

Note that endstops / filament sensors that are wired normally open (NO) frequently require `^` (pull up resister) to correctly function.
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

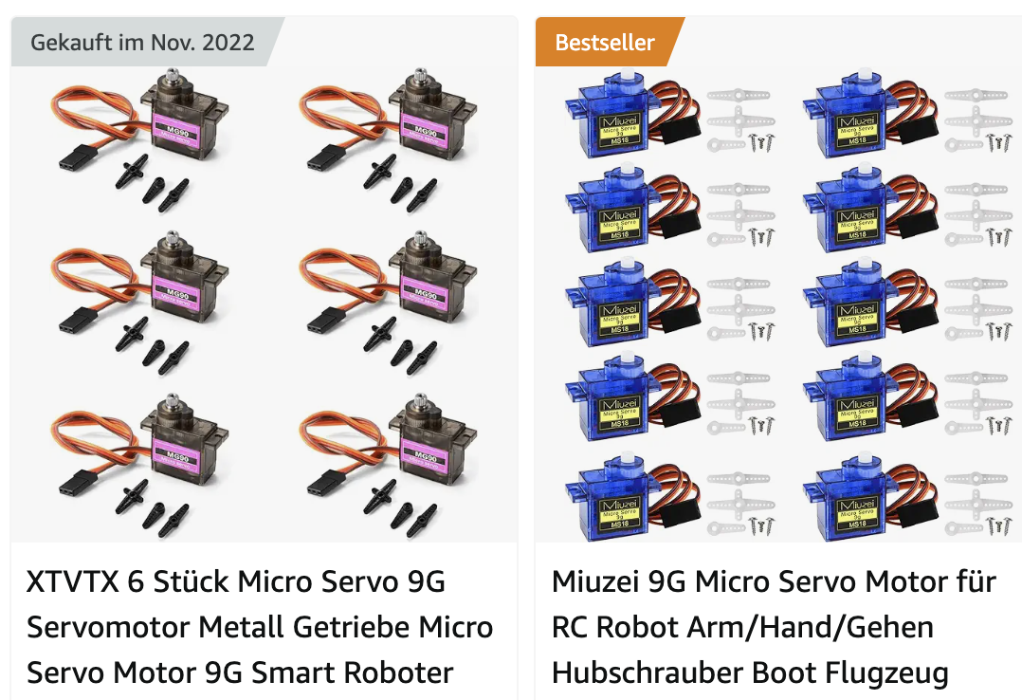
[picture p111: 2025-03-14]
Documentation/assets/servo_testing/CleanShot_2024-05-02_at_21.44.022x.png

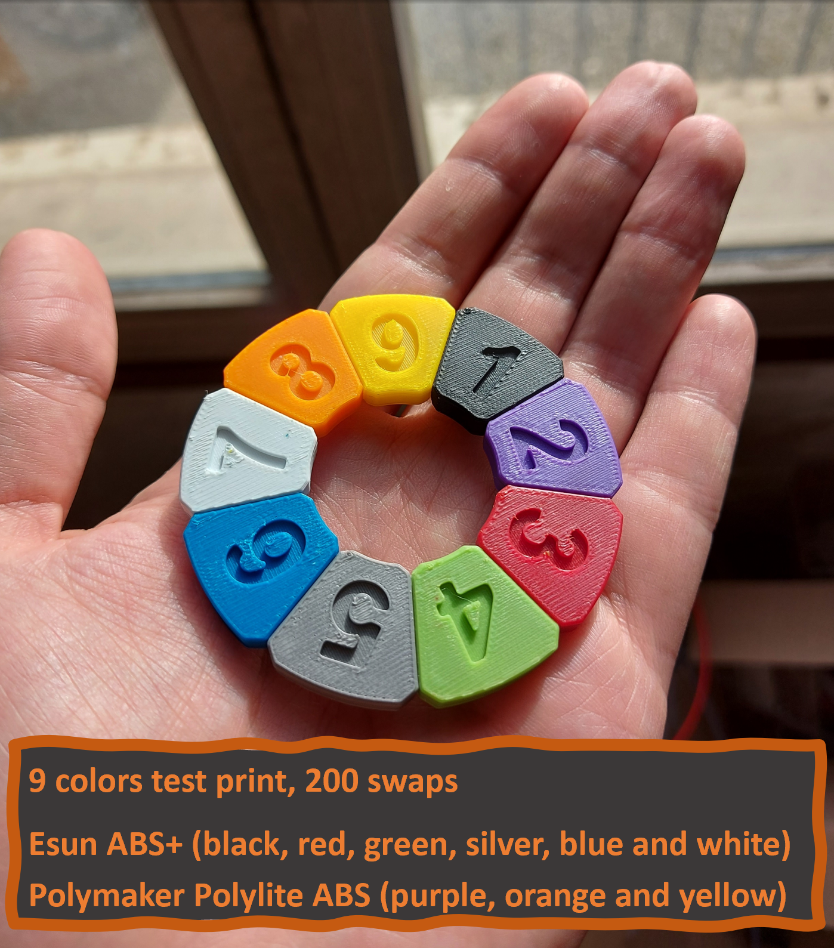
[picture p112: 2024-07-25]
Assets/Showroom/9_colors_test.png

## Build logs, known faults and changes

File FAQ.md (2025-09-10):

# ERCF v3 FAQs
To be filled out once we know what the FAQs are!

# ERCF v2 FAQs

### Q1. Will there be kits available for ERCF V2, and where can we get them?
LDO and  a number of vendors will have kits available for ordering in the coming months. Full kits will be available sometime in late 1st quarter of 2024.

### Q2. I bought an ERCF v1.1 kit. Will this be compatible?
ERCF v1.1 kits will be compatible with V2 with some additional hardware and fastener kits. We have made every effort to utilize as much of the original kit as possible. Upgrade kits will be available at various select vendors in the coming months. Be aware the kits will be less a single channel for the V2 upgrade to accommodate the wider filament blocks.

### Q3. Will ERCF come with a filament cutter?
ERF (Enraged Rabbit Filametrix) has been developed and optimized to work with ERCF V2. Although dozens of toolhead designs exist, the initial launch will be based on the Voron Stealthburner with Clockwork 2. There are numerous versions of toolheads, and the library of STLs will be expanding to support the greater community. We also encourage the public to develop and test their versions and to submit them to be included in our collection. More extruders are being actively developed and will be released in the coming months.

### Q4. I see that ERCF comes with a built-in buffer. Is this required or optional?
Enraged Rabbit Cotton Tail (ERCT) has been specifically designed to give the best multi-filament experience for V2; however, it is completely modular and optional for your build. You can choose to use other buffer designs; our software design is flexible. One of the stand-out features of ERCT is the ability to use a pre-gate sensor, which is designed specifically to improve Endless Spool performance.

### Q5. Do I have to order a kit, or can I self-source this? Is there a BOM?
Kits are expected to be available in the 1st quarter of 2024. Our BOM will list all the parts needed with a wizard to help you customize the kit to your requirements. The BOM will be found through our GitHub listing with links to vendors who can provide parts for self-sourcing.

### Q6. When and where will the v2 BOM be located? Is it with the same BOM as V1.1?
The V2 BOM will located on the GitHub page after RC1 has been released. This will be at a new location, not the old ERCF V1.1 site.

### Q7. What tool heads will this support?
Initially, ERCF V2 will be released with ERF (Filametrix) for Voron Stealthburner CW2 toolheads. Active development and collection of many popular hotends to companion with it is underway and will be part of the GitHub Repository. Alternative extruders are also being developed or being sourced with a cutting head. ERCF V2 also supports sensorless systems but is less reliable than a filament-cutting solution.

### Q8. Is the BTT MMB board required, or will older Easy BRD still work with V2? 
BTT MMB is the new standard and recommended board for V2. Easy BRD and alternatives will work for most of V2's features, but some of the new features, like pregate sensors and, in some cases, RGB lighting, will require a board with enough endstop and LED inputs to operate fully.

### Q9. Where can I get support for my ERCF V2 build?
ERCF V2 is built on a community of supporters and other experienced builders. Visit [VoronDesign #ercf_questions](https://discord.com/channels/460117602945990666/909743915475816458) Discord server for any questions and support issues where members of the V2 team as well as the community is there to help.

### Q10. Is there a build guide on assembling and calibrating my new ERCF?
Yes, a build guide is available in PDF format on the GitHub repository.

### Q11. Will ERCF V2 work with other non-Voron printers?
ERCF V2 currently works with most Klipper-based printers. The current exceptions are sandboxed builds of Klipper made proprietary by some companies and do not have the ability to add third-party software. Consult your product's support pages to see if there are ways to add third-party add ons, which may allow you to install the necessary software for ERCF V2 to work with your printer.

### Q12. I modified by V1.1 with TripleDecky, SturdyBunny, Springy, etc.  Do I already have a ERCFv2?
No. While ERCFv2 incorporates many "beta" modification projects from the team, it also includes many refinements, some subtle and some not.  These changes were all necessary to guarantee ERCFv2 would work together.  The only exception to this is that TripleDecky C7.0 filament blocks are identical to those in ERCFv2.  Other than those you are strongly encouraged to reprint and re-build to ensure you have a supported platform. In addition Happy Hare, with a vendor and version set to "ERCF" and "2.0" will correctly support ERCFv2 but this mode will not necessarily work with a heavily modified v.1.

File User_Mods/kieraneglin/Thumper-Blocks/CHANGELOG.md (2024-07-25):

# Changelog

## Rev 3 (2023-12-15)

All parts except the latch have been modified and are not compatible with previous revisions.

- Beefed up M4 holder to prevent breakage during M4 installation
- Beefed up filament path side walls to prevent breakage during ECAS installation
- Removed 2 layers of width from the filament path to reduce the chance of rub when installed
- Updated base to support roll-in inserts for mounting to the rail
  - Also moved mounting hole just a bit
- Improved magnet fitment on filament path
- Added channel in base to improve filament feeding reliability

**UPDATE (2024-01-01)**

- Added `Thicker` variant to support ERCF v2 spec
- The original `Rev 3` is now in the `Thinner` directory
- The `filament_path` and `base` files are changed and not compatible between variants. The latch and tophat are unchanged.

## Rev 2 (2023-11-10)

- Updated tophat and filament path to use a two-landing design for the `up` vs. `down` positions. This makes the `up` position more reliable and repeatable. Don't forget to use the Springy servo arms!
- Updates some chamfers on the base (inconsequential)

## Rev 1 (2023-08-15)

Initial release!

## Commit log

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2024-08-04 Updated Files
    Several small file updates for Gearbox anticrush feature, 5mm coupler, add some experimental files, renames and moves.
    [BARF_Holder.stl, Bearing_Guide_for_Direct_Driveshaft.stl, Bearing_Guide_for_Geared_Driveshaft.stl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]
2024-08-04 Update [a]_Drag_Chain_Anchor_Bottom.stl
    Fixed mount holes to right diameter
    [[a]_Drag_Chain_Anchor_Bottom.stl]
2024-08-04 Added f3d and step of beta split coupler
    Print two. Heatsets go in the 4.7mm holes
    [[a]_5mm_Split_Coupler_V0.f3d, [a]_5mm_Split_Coupler_V0.step]
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2024-08-13 Create Filament_path_C9U1_xN.stl
    Fix for M2x10 SHCS
    [Filament_path_C9U1_xN.stl]
2024-08-13 Update TD ( fix for M2x10 SHCS
    [Base_xN_v2.stl, Filament path C90_xN.stl, Filament path_xN.stl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]
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2024-08-17 New CAD and STLs
    New CAD and STLs incorporating lots of individual contributions.
    [Base_xN_C9U1.stl, End_Block_v3.stl, Filament_path_xN_C9U1_repaired.stl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]
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2024-09-20 Update [a]_Tophat_xN_vC9.3.stl
    Fix print orientation
    [[a]_Tophat_xN_vC9.3.stl]
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2024-11-20 CAD Update and New Parts - LED Connector
    Added LED connector slot to Gearbox and Foot.
    [Gearbox_v4.stl, [a]_Gearbox_Foot_v4.stl]
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2025-02-27 Reorganization and Renaming
    Reorganized and renamed files. Added new versions of Motor Mounts, Gearbox, and Gearbox LED.
    [2020_Mount.stl, 2020_Mount_Mirrored.stl, 3030_Flat_Mount.stl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]
2025-03-05 Minor reorganization
    Just changing file paths / names and adding the 10mm idler version.
    [80T_Cog_Guide.stl, Calib_Test.stl, Calib_test_For_C9.stl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]
2025-03-06 Added copies of Happy Hare documentation
    Copied the necessary setup pages from the Happy Hare wiki. Started to make them ERCF-flavored, but there's a lot more to do.
    [Beta_BOM_v0.9.csv, Beta_BOM_v0.9_Geared.csv]
2025-03-06 New CAD and STL updates
    New CAD, new End_Block, oriented Selector STL for printing, add MMBv2 box lid.
    [End_Block_v4.stl, Lid.stl, [a]_Selector_Cart_v2.8.stl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]
2025-03-06 Update the links in Quick Start
    Update the links in Quick Start, also fixed a link in Setup Calibration
2025-03-08 Cleanup for Beta testing crew
    Deleted a bunch of old and extraneous files to prep for Beta testing
    [Calib_Test.stl, End_Arm_Cap_Mount.stl, End_Arm_Cap_Mount_Extension.stl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]
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2025-03-09 Update Gearbox.stl
    Widened the reinforcement cutout slots, because slicers were ignoring them (again).
    [Gearbox_v6.stl]
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2025-03-10 Top hat with correct print support
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2025-03-10 Update Hardware-Calibration.md
    Fixed links, minor verbiage
2025-03-10 Update Hardware-Calibration.md
    Fixed another link.
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2025-03-10 Update Installing-KlipperScreen.md
    Fixed links
2025-03-10 Create [a]_Selector_Cart_v2.81.stl
    Fixed the support for this STL.
    [[a]_Selector_Cart_v2.81.stl]
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2025-03-10 Update [a]_Selector_Cart_v2.81.stl
    Flipped to printing orientation.
    [[a]_Selector_Cart_v2.81.stl]
2025-03-10 Added Rumout Buffer and Universal Box with MMB V2 compatability.
    Formerly Cotton Tail Lite and pregate switches, the renamed runout buffer is what makes endless spool, runout and pre loading work on the ERCF.
    Third party buffers should also be paired with this to ensure full compatibility with Happy Hare.
    This revision has had a small increase in runout buffer to 14.6mm which will increase the tolerance and reliability of endless spool.
    All standard V2 kits have the required components for this so no additional hardware will be necessary.
    [Box_Lid_Universal.stl, Box_Standoff.stl, Box_Universal.stl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]
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2025-03-11 Renamed Runout Buffer Coupler Block
    It needed to have the _xN suffix.
    [Runout_Buffer_Coupler_Block_xN.stl]
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2025-03-11 Update Hardware-Calibration.md
    Added details and fixed typos
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2025-03-11 Update Documentation
    Added warning about rotation distance to hardware calibration page, fixed verbiage on config checks page.
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2025-03-11 Create Base_v03.stl
    Quick fix for the MMBv2 base
    [Base_v03.stl]
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2025-03-12 Create Gearbox_v61.stl
    Fixed the support that Fusion helped mess up.
    [Gearbox_v61.stl]
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2025-03-13 Reorganizing and adding ERCT V3
    ERCT V3
    Changes from V1 to RC2
    - Changed to a modular multipart arm design
    - Added Alignment pins between buffer walls
    - Arm mount integrated to lower arm part (reduced some parts)
    - add larger funnel on Coupler Block for easier loading
    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
    [Axle_4_Double_Thread.stl, Axle_8_Double_Thread.stl, Axle_Hex_8.stl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]
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2025-03-13 Update Logo_Mask_v32.stl
    Fixed print orientation
    [Logo_Mask_v32.stl]
2025-03-13 Fix Print Orientation
    [Motor_Mount_NEMA14_Metal_80T_v4.stl, Motor_Mount_NEMA14_Printed_80T_v4.stl, Motor_Mount_NEMA17_Metal_60T_v4.stl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]
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2025-03-14 Additional Axle for 9 and 12
    9, 12 and segmented 12 gate axles added.
    [Axle_Hex_12.stl, Axle_Hex_12_segmented_1-2.stl, Axle_Hex_12_segmented_2-2.stl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]
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2025-03-15 Create Toolhead-Distances.md
    Forgot a page! Links to be fixed soon
2025-03-15 Update Hardware-Calibration.md
    Seeing if this fixes Mermaid
2025-03-15 Fix links and add images for Toolhead Distances page
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2025-03-15 Updated DD Motor Mounts
    Removed a small ridge that was causing problems from both DD motor mounts.
    [Motor_Mount_NEMA17_Direct_Drive_v81.stl, Motor_Mount_NEMA17_Pancake_Direct_Drive_v31.stl]
2025-03-15 Small updates
    notes about how the servo down command deliberately makes the Gear motor twitch.
2025-03-16 Tweaks to ERCT V3
    Split 12 gate axis - added registration channels
    Coupler Blocks - adjustments to print supports
    LED Carriers - adjusted tolerance to be less loose.
    [Axle_Hex_12_segmented_1-2.stl, Axle_Hex_12_segmented_2-2.stl, Coupler_Block_V6B_Base.stl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]
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2025-03-18 Updated CAD for ERCT V3 and increased tolerance for locking buffer hub.
    [Locking_Buffer_Hub_Printed_Axial_xN.stl]
2025-03-19 Printable Cable Chain Updates
    Updated printable cable chain files to be shorter. Added middle section and 3MF files.
    [Printable_7x7_CableChain_Middle.3mf, Printable_7x7_CableChain_Middle.stl, Printable_7x7_CableChain_Side_A.3mf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]
2025-03-19 Update PTFE_Tool_631mm.stl
    Fixed depth problem
    [PTFE_Tool_631mm.stl]
2025-03-20 Create MM_Test_8_color_v1.3mf
    New test print option for 8 colors. First version, may change.
    [MM_Test_8_color_v1.3mf]
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2025-03-27 Added revision B of experimental Filament block
    Some housekeeping as well as latest edition of Filament block.
    [Box_Universal.stl, Filament path_9.4B_xN.stl, Filament_path_C9.3B_xN.stl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]
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2025-03-29 Update Hardware Calibration
    Fixed a typo and some verbiage in the MMU_CALIBRATE_BOWDEN section
2025-03-31 Development edition of Filament Path with Sensor switch
    Sensor Switch Filament Path Block
    This is the micro switch edition of the filament path block. This now adopt sthe use of levered switches, MR85 bearings, and should replaces the need for the runout buffer for Filamentalist.
    This should only be used as a dual paralell switch configuration for ERCT or for Filamentalist. It is not reliable for endless spool runout. If a thirdparty buffer is used (pika, quiver, etc....) the runout buffer should be used instead of this option.
    Wiring of this is recommended to be soldered at right angles and inline with the filament path, with a pigtail header wire so it's easy to connect.
    [Filament_path_C9.5S_xN.stl]
2025-04-05 Create Gearbox_v61_for_M6.stl
    User mod for people who need to use an M6 instead of an M5 for the Gearbox.
    [Gearbox_v61_for_M6.stl]
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2025-04-05 Isolated Split Coupler
    A version of the Split Coupler with isolation between the motor and deice shafts, for static charge mitigation.
    [[a]_Split_Coupler_A_isolated.stl, [a]_Split_Coupler_B_isolated.stl]
2025-04-05 New COAS mount
    New version of the COAS mount for front-facing ERCFs.
    [COAS_Lens_Bracket_0-3.3mf, COAS_Lens_Bracket_12-15.3mf, COAS_Lens_Bracket_4-7.3mf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]
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2025-04-05 Delete Base_xN_C9U2.stl
    Revert to U1 - U2 was not an improvement.
    [Base_xN_C9U2.stl]
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2025-04-06 Revert "Delete Base_xN_C9U2.stl"
    This reverts commit 6d17a5ebd68dea083db2c6c3066584ca9bd32f6d.
    [Base_xN_C9U2.stl]
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2025-04-09 Added Levered Switch (6x3 Bearings) Filament block
    All three versions have additional print supports in them.
    [Filament path_9.7B_xN.stl, Filament_path_C9.7BL_xN.stl, Filament_path_C9.7BM_xN.stl]
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2025-04-09 Update [a]_Selector_Cart_v2.9.stl
    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
    [[a]_Selector_Cart_v2.9.stl]
2025-04-11 Flipped Selector Motor Mount
    Motor mount for flipped Selector Motor, ie motors larger than 20mm.
    [Linear_Axis_Selector_Motor_Support_Flipped.stl, Linear_Axis_Selector_Motor_Support_Flipped_Precise.stl]
2025-04-11 Add bridging for round holes
    Added bridging fix to round vertical holes.
    [Linear_Axis_Selector_Motor_Support_Flipped.stl, Linear_Axis_Selector_Motor_Support_Flipped_Precise.stl, Linear_Axis_Selector_Motor_Support_Precise.stl]
2025-04-12 Split Coupler Cleanup and New B Version
    -removed the unisolated couplers
    -Added v2, with 7mm diameter hole for an M3 washer
    [[a]_Split_Coupler_A.stl, [a]_Split_Coupler_B.stl, [a]_Split_Coupler_B_isolated_v2.stl]
2025-04-12 New C9.8 Filament Blocks
    **Filament Block C9.8**
    Change Log
    - increased filament path from 2.0mm to 2.2mm (make sure you do not use Capricorn tubes on this, it will jam. You should be using ID 2.2-2.5mm PTFE (tubes)
    - print supports on filament path (added in C9.7)
    - new universal switch (accepts no lever or levered micro switches)
    - can accept all kinds of bearings from 8x3, 8x2.5, 6x3, and 5.5 ball
    - printable lever for those that have removed and lost levers
    - printable adapter for smaller bearings.
    [Bearing_Adapter_5.5_xN.stl, Bearing_Adapter_6x3_xN.stl, Filament_path_C9.8BL_xN.stl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]
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2025-04-15 Create [a]_Customizable_Split_Coupler_B.3mf
    Customizable Split Coupler created for shaft flat depths at 4.0, 4.1, 4.2, 4.3, 4.4, and 4.5mm (default).
    [[a]_Customizable_Split_Coupler_B.3mf]
2025-04-15 v2 Idler Blocks
    Improved v2 Idler Blocks with indicators, room for ProModeler and other big servos by default, and updated version number. 10mm edition also updated in User Mods.
    [Linear_Axis_Idler_Block_for_10mm_Idlers_v2.stl, Linear_Axis_Idler_Block_v2.stl]
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2025-04-15 Added Rod Sights to the Mounts
    So you can tell when your rod is at the right depth. Applied to all Selector motor mounts.
    [Linear_Axis_Selector_Motor_Support_Flipped_Precise_v2.stl, Linear_Axis_Selector_Motor_Support_Flipped_v2.stl, Linear_Axis_Selector_Motor_Support_Precise_v2.stl]
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2025-04-17 Updated Base and Brakes
    Updated the Base to align the Brakes better, move the version number, alignment line, and printability improvements.
    Updated the Filament Trap and Filament Brake to center the mounting hole and make it fit better generally.
    [Base_xN_C9U4.stl, [a]_Brake_B2_xN.stl, [a]_Trap_M3x2_xN.stl]
2025-04-19 Cleanup Filament Blocks folder
    Removed old versions of files that are no longer needed.
    [Base_xN_C9U1.stl, Base_xN_C9U2.stl, Filament_path_xN.stl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]
2025-04-19 Clean up Tools Folder
    Removed old files that are no longer needed.
    [Pulley_Tool_NEMA14.stl, Pulley_Tool_NEMA17.stl]
2025-04-19 Clean up Motor Mounts Folder
    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
    [Logo_Mask_v3.stl, [a]_Split_Coupler_B_isolated.stl]
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2025-04-19 Update Linear_Axis_Selector_Motor_Support_Precise_v2.stl
    Fixed printing orientation.
    [Linear_Axis_Selector_Motor_Support_Precise_v2.stl]
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2025-04-19 ERCT V3_Rev 2 Update
    **ERCT V3 Revision 2 CAD Complete**
    Changes to this version from the first revision of V3
    - Mount arms now have clearance for JST headers and plugs for the dual switch filament blocks
    - New passthrough holes on arms for wire management
    - Coupler blocks eliminated (but pins are still there in case people prefer to use them still)
    - Coupler pins have a new angle on them to better meet the filament block angle and the buffer's increased size.
    - New replacement switch location, integrated into buffer arm (same switch design as filament block). Should reduce friction further. Can be located in any three locations.
    - New support arm integrated into the bypass block for end-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
2025-04-26 Create ERCFv2.5_Manual_04-26-25.pdf
    New manual. Better belt installation pages, added lots of small details, added wiring page links, lots of typos fixed.
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2025-05-04 Create MMB_mount_hinge.stl
    Missed a file!
    [MMB_mount_hinge.stl]
2025-05-04 **C10 Filament Block**
    - Gears have been relocated and optimized in the block design to be spaced optimally for correct filament pressure
    - Idler gear is now integrated into the filament body reducing printing variations/errors that were stacked in the previous design.
    - Reduced interface points. Elimination of catch points with the elimination of brake/trap holes.
    - Reduced wide openings. Giving far better stability to the filament so it does not miss the encoder hole.
    - Elimination of the old brake/trap. This has now been removed and relocated.
    - Redesigned 2 part Latch design. Latch now acts as a 'parking' brake for preventing filament from drifting. 2nd part is replaceable, a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
    [Base_C10_U5_xN.stl, Top-Hat_C10_xN.stl, [a]_Latch_C10_xN.stl]
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2025-05-04 Update ERB_Box_Lid_v01.stl
    Flipped to print orientation
    [ERB_Box_Lid_v01.stl]
2025-05-04 Update EASY_BRD_Lid_v01.stl
    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
    [EASY_BRD_Lid_v01.stl]
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2025-05-06 Revision 2 Updates
    - Three Base Block options (P) Steel pin, (S) M2 Screw, and (F) PLA or PETG Filament (do not use ABS)
    - Corrected base widths to 23.05mm Standard
    - Adjust 2020 key profile to better accept Roll-in nut and maintain universal registration with variations on 2020 extrusions
    - Fixed Manifold Errors on Filament Block
    - Adjust Tolerance void on Filament Block
    - Fixed Print supports on the Filament Block
    - Other minor geometry clean up and corrections.
    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
    [Base_C10_R2F_U5_xN.stl, Base_C10_R2P_U5_xN.stl, Base_C10_R2S_U5_xN.stl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]
2025-05-06 v2 of ERB Electronics Box
    -Added 0.25mm of clearance so that the board doesn't strain when removed
    -Added 4mm of height to the lid to clear the stepper driver heatsinks
    -Thickened the lid mesh from 0.6mm to 1.0mm to make it sturdier
    [ERB_Box_Base_v02.stl, ERB_Box_Lid_v02.stl]
2025-05-06 Update Lids, add Long Hinge
    -Updated all lids to be thicker (0.6mm to 1.0mm)
    -Added the Long Hinge for clearance of the Linear Axis, if desired.
    [EASY_BRD_Lid_v02.stl, ERB_Box_Lid_v02.stl, MMBv1_Box_Lid_v03.stl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]
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2025-05-10 New versions
    Updated versions with small tweaks. Fixed the Revo Front to have the Filametrix mods.
    [CW2_Main_Body_ET_Sensors_ECAS_v4.stl, CW2_Main_Body_ET_Sensors_PC4-M10_v3.stl]
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2025-05-11 C10 Rev 4
    C10 Revision 4
    Base Block - Recommended replaced from Rev 3
    - Removed 2020 Indexing part and replaced with sidewalls. This should make it compatible with any 2020 Extrusion and any compatible Roll-in T-Nuts.
    - Added partial printed threading for hinge. Can accept either M3x20 SHCS or Pin
    Top Hat - Cosmetic/printability improvements not required replacement for Rev 3
    - Small Overhang improvements (change of angles)
    - Flipped hinge so it doesn't require print supports
    Filament Block - Cosmetic/printability improvements, not required replacement for Rev 3
    - Printability improvements including, better BMG void supports and small geometry corrections.
    - Small geometry adju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
    [Base_C10_R4_U5_xN.stl, Encoder_Left_v25B.stl, Filament_Block_C10_R4_xN.stl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]
2025-05-11 Create CW2_Main_Body_EBB_2240_ET_Sensors_ECAS_v3.stl
    Added the previous modifications and reworked the EBB 2240 cable door part.
    [CW2_Main_Body_EBB_2240_ET_Sensors_ECAS_v3.stl]
2025-05-11 Encoder v25B_R2
    Revision 2 update. Added bevels to give it more clearance and move across blocks.
    [Encoder_Left_v25B_R2.stl, Encoder_Right_v25B_R2.stl]
2025-05-12 Small printability tweaks
    Small print support improvements. Do not need to replace previous versions for this.
    [Base_C10_R4_U5_xN.stl, Filament_Block_C10_R4_xN_no-switch.stl, [a]_Latch_C10_one-piece_xN.stl]
2025-05-13 Corrected exported files
    Turned off additional hardware on exports. Also added a M5 option for the 625 bearings so no need for a bushing.
    [Encoder_Left_v25B_R2_M5.stl, Encoder_Right_v25B_R2.stl, Encoder_Right_v25B_R2_M5.stl]
2025-05-13 Update Encoder_Left_v25B_R2_M5.stl
    adjusted tolerance
    [Encoder_Left_v25B_R2_M5.stl]
2025-05-16 Update Encoder_Right_v25B_R2.stl
    Updated to the correct file.
    [Encoder_Right_v25B_R2.stl]
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2025-05-20 Cleaned up directory - Correct STLs
    Cleaned up the directory and added the correct STLS for the halves.
    [688-Bushing.stl, Encoder_Left.stl, Encoder_Left_v25B.stl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]
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2025-05-24 Update Encoder_Right_v25B_R3_M5.stl
    Correct M5 part
    [Encoder_Right_v25B_R3_M5.stl]
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2025-06-13 Update ERB_Box_Base_v03.stl
    Replace with correct file
    [ERB_Box_Base_v03.stl]
2025-06-19 Update ERB_Box_Lid_v03.stl
    Replace with correct file.
    [ERB_Box_Lid_v03.stl]
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2025-07-14 Filament Path R7
    Filament Path R7 with corrected switch, MR85zz bearing, and printed lever cavities.
    [Filament_Path_C10D_R5.stl, Filament_Path_C10D_R7.stl]
2025-07-19 Experimental Jack Rabbit - Servo Replacement Mod
    [BRAKE_Lever_xN.stl, Servo_replace_jack_rabbit.stl, Top-Hat C10-JR_xN.stl]
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2025-07-27 Swap Brake Options
    The Brakeless option is now the main option
    [BRAKE_Lever.stl, [a]_C10_Latch R6.stl.stl, [a]_Latch_C9_xN.stl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]
2025-07-29 Updates for Filament Block
    Changes to the Base:
    -Allowed the hinge to open to 120 degrees (from 90) for easier maintenance
    -Deepened the Latch screw hole so that 10-12mm bolts may be used.
    Changes to the Filament Path:
    -Tilted the rear face to 10 degrees (from 4) so that the Encoder won't hit it when disengaged.
    -Made the Antisquish threads 5mm long (from 3).
    [Base_C10D_R3.stl, Base_C10D_R4.stl, Filament_Path_C10D_R7.stl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]
2025-07-29 Update to Fiilament Blocks
    Fixed 120-degree opening feature
    [Base_C10D_R4.stl, Filament_Path_C10D_R8.stl]
2025-07-29 Update Filament_Path_C10D_R8.stl
    Fixed a Fusion360 glitch
    [Filament_Path_C10D_R8.stl]
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2025-08-05 Filament Path Updates
    New Lever.
    R9 / R5 was short-lived.
    Accommodations for suboptimal printing:
    Magnet holes are 0.1mm deeper
    Larger hinge bolt passageway
    [Base_C10D_R4.stl, Base_C10D_R6.stl, Brake_Lever_R3.stl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]
2025-08-06 Rename
    I swapped the names, whoops
    [BOM_08-05-25.csv, BRAKE_Lever.stl, Brake_Lever_R3.stl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]
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2025-08-30 Update Filament_Path_C10D_R10.stl
    Fixed the supports that Fusion broke.
    [Filament_Path_C10D_R10.stl]
2025-08-30 Update Filament_Path_C10D_R10.stl
    Fixed the support again.
    [Filament_Path_C10D_R10.stl]
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2025-09-10 Flipped Motor Support to User Mod Standards
    [Linear_Axis_Selector_Motor_Support_Flipped.stl, Linear_Axis_Selector_Motor_Support_Flipped_Precise.stl, Linear_Axis_Selector_Motor_Support_Flipped_Precise_v2.s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]
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2025-10-18 Update Servo Sleds
    Update to correct orientation with supports
    [Servo_Mount_DS041MG_v2.stl, Servo_Mount_General_v2.stl, Servo_Mount_Savox_v2.stl]
2025-10-23 Fix Filenames
    [Base_C10D_R6_xN.stl, Filament_Path_C10D_R10_xN.stl, [a]_TopHat_C10D_R1_xN.stl]
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
